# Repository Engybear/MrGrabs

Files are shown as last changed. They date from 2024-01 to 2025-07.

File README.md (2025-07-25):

# MrGrabs
<div align = "center"> 
  
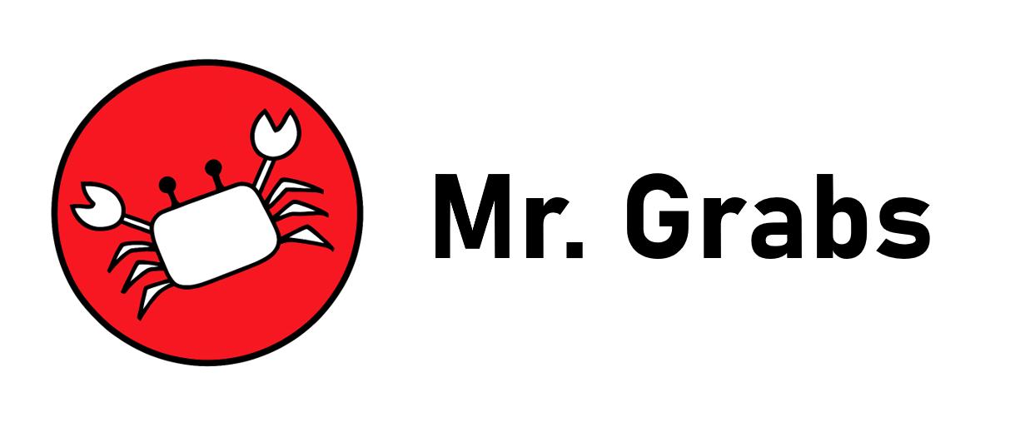
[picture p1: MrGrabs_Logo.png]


</div>

<!-- TOC -->
* [MrGrabs](#mrgrabs)
  * [Inspiration, Purpose and Goals](#inspiration-purpose-and-goals)
  * [What It Does / Overview](#what-it-does--overview)
  * [File Organization / How It's Made](#file-organization--how-its-made)
  * [Challenges Faced](#challenges-faced)
  * [Accomplishments To Be Proud Of](#accomplishments-to-be-proud-of)
  * [Next Steps](#next-steps)

## Inspiration, Purpose and Goals
This project was inspired by a professor's desire to ride around the University of Toronto campus inside and outside buildings on a robot that could wave to students with mechanical arms.

After scaling down the scope of the project to fit within a provided budget of $1000, the primary objective of this project was to build a robot that would complement another research project that involved the use of artificial intelligence for facial and voice recognition on a computer. With this in mind, the robot was designed with a laptop mount, but to further ability to interact with humans, it was also given the capability to navigate through conventional doorways inside buildings of the university campus and to mechanically interact with humans through pre-programmed robotic arm gestures. 

As a secondary objective during construction, the approach of pushing the limits of the quality of the final product with as minimal expense as possible was taken.

## What It Does / Overview
MrGrabs is a medium-sized (16x16x20'') robot, capable of driving through doors with at lest 2' of clearance. It is built primarily out of PLA, with plexiglass and wood used to reinforce the chassis. The robot is controlled via a custom bluetooth APP on an Andriod phone, and integrated with a Microsoft Surface Pro running an application of another project to scan for, greet and wave to students on campus. It also has four HC-SR04 Ultrasonic Sensors that are unused but intended to be a safety feature to prevent collisions.

<div align="center">
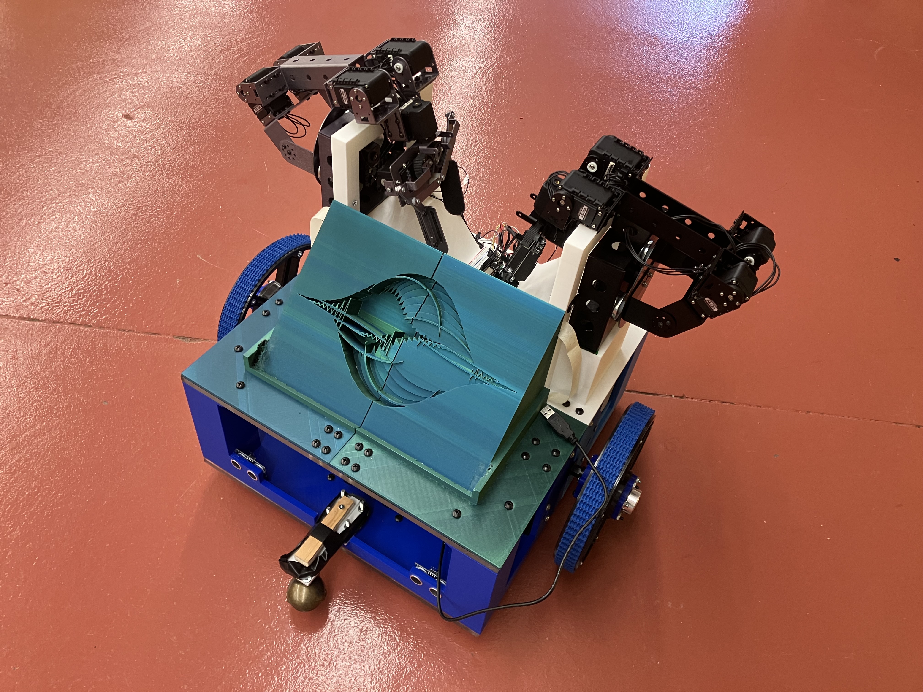
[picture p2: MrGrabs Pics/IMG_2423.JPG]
  
  
</div>

### Design Breakdown
Here you can see an overview of the design. The phone connects to the principal controller of the robot (Arduino Nano 33 BLE), which directly manages the motors through the IRF3205. There are also 2 agent controllers, as the Adafruit Feather 32u4 BluefruitLE, that receive simple commands from the principal controller, which are individually used to control the 2 robotic arms, made up of 7 daisy chained AX12-A servos. The Arduino Nano itself is powered by and can recieve data from a mounted laptop, if desired. Lastly, there are HC-SR04 sensors that can be controlled by the Arduino Nano as well to lock up the motors if a collision is imminent.

<div align = "center"> 
  
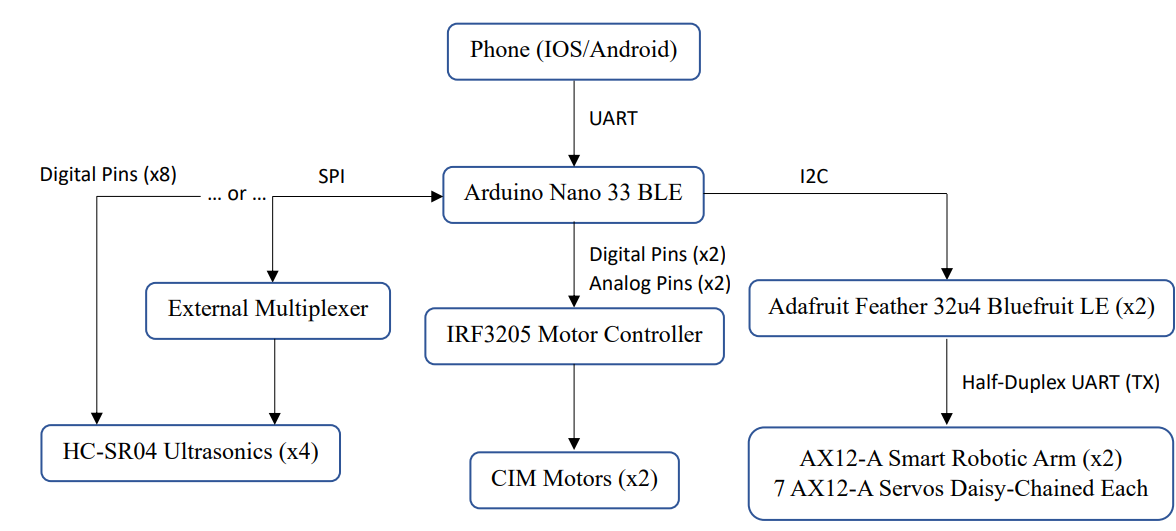
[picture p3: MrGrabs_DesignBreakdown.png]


</div>

- Refer to MrGrabs Pics for more images of the robot

## File Organization / How It's Made

Refer to User Guide for setup and usage information

Refer to Construction Guide for system design information

Refer to ArduinoCode/MainSketches for the code controlling the robot's code written in `C++`

Refer to BluetoothApp for the BLE5.aia file used to configure the andriod app remote controller created through `MIT App Inventor`

Refer to Step and Print files for CAD design and 3D printing files created in `Fusion360`

## Challenges Faced
The major challenge during the construction of the robot was maintaining a low budget while designing the robot’s chassis to support the forces it would experience. Although the original design was entirely 3D printed plastic, additional materials of plexiglass and wood were scavenged and machined to be worked into the robot’s design. The plexiglass was required because the weight of the robot's components would bend the plastic. The wood was required after the original high-density plastic mounts for the castor wheels snapped under both the weight and the torque of the robot starting and stopping motion.

Another challenge faced was the timeline given to develop the robot being 6 weeks. That is 6 weeks to plan the design, 3D model, 3D print, physically acquire, construct, and machine the chassis and its components parts, program multiple on-board controllers in an embedded system, build a remote bluetooth controller app from scratch, do the final stages of testing, making adjustments / deal with setbacks where needed and finally write up the documentation / user guides. Needless to say, the design isn't perfect. The motors were over-engineered and can go much, much faster than the robot needs to under its current weigh of ~30lbs, while the supports for the castor wheels under-engineering and snapped during intitial tests.

Lastly, it should be noted that the robotic arms were taking from a lab that had shelved them, from being outdated. They are at least 10 years old and during operation if the robot moved to quickly while the arms were not stowed, the arms' servos would not be able to hold up their own weight or complete their set path while under external torques. Additionally, with the equipment I had available, I was only able to create a half-dupliex communication line between the Adafruit boards and the robotic arms, to either read current positions or set goal positions. not both at the same time. As such the Adafruit boards had to rely on delays to roughly estimate when a motion would be complete, compounding on the limitations of the robotic arms in the design.

## Accomplishments To Be Proud Of
With this being only my second year of university, this was my first attempt at solo-developing a robot, first time trying to print something this big, first time creating a bluetooth controller app, and many other firsts (granted many thanks are owed to the people who provided me with the resources and advice to make this happen), I believe it's an accomplishment in and of itself to have finished a working design within both the set budget and timeline.

It pleases me to know that 2 years later, the project has not been shelved but been passed on to another research student who is working on extending the chassis in height to make the robot larger and more humanoid and fully integrate the sensors and AI code into the controller for the robot. It is possible that we might see a prototype rolling around the university campus in the summer or a capstone team working on the design, as the project continues to develop towards an interactable lecture attendance keeper.

## Next Steps
1.	It is HIGHLY recommended in the future that for a project of this scale, to allot more than 6 weeks and a single person to work on the project, for the sake of allowing more time to think through the design in its initial phases, different ideas to come up from different people, and minimize oversights.
2.	It is HIGHLY recommended that stronger mounts for castor wheels are designed in any new design iterations of this robot, as that is the robot’s biggest current design weakness and point of failure during operation.
3.	It is HIGHLY recommended that if the design is to be 3D printed again, methods be implemented to reduce the use of supports as much as possible, while taking into consideration the structural integrity of the design. Reducing the use of supports, both reduces the costs spent on materials and reduces the printing time of each piece, which can make the difference between printing 1 piece or 2 pieces in a single day. Talk to the person who is managing the 3D printer you want to use, for ideas.
4.	It is recommended to look into methods of recharging the robot’s 12V and 4V battery, as the Energy Systems Lab currently does not have a battery charger, as of 2023. The professor has stated that using a DC power supply to charge the battery is viable.
5.	It is recommended to invest in a Roborio for both now and all future projects, rather than using Arduino or Adafruit boards, as a Roborio can support several different kinds of I/O at a processing speed much faster than an Arduino/Adafruit board would be able to provide.
6.	It is recommended to swap out the bolts on the bottom of the robot for shorter 1’’ ones to allow for more clearance underneath the robot.
7.	It is recommended to find a different method of wiring hardware parts of the robot together, as to not use cheap/old jumper wires and solder to hold them together under heat shrink.
8.	It is also recommended in future design iterations to allow more time to think about wiring and include design features like hooks to help secure wires down.
9.	It is recommended that if the Ultrasonics Sensors are to be wired up to the Arduino Nano 33 BLE board, that an additional SPI multiplexer chip is used to reduce the number of digital pins used up by the Nano. This is to leave room for potential future additions.

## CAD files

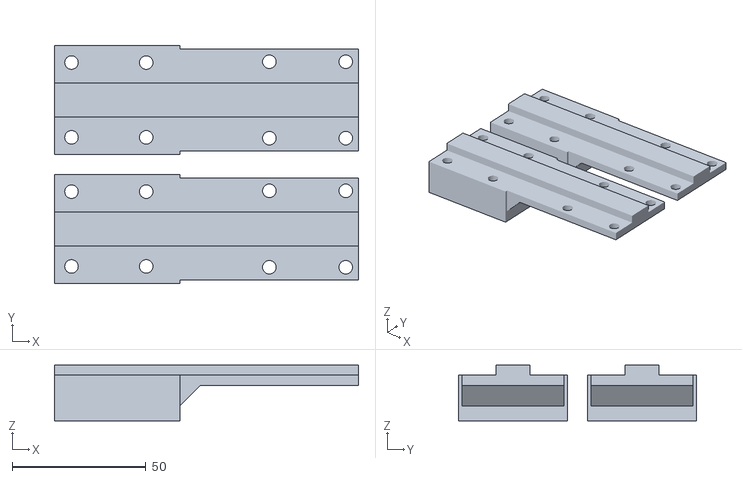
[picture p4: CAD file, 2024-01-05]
CAD_PrintFiles/MountsSection2.stl
113.7 x 88.9 x 20.9

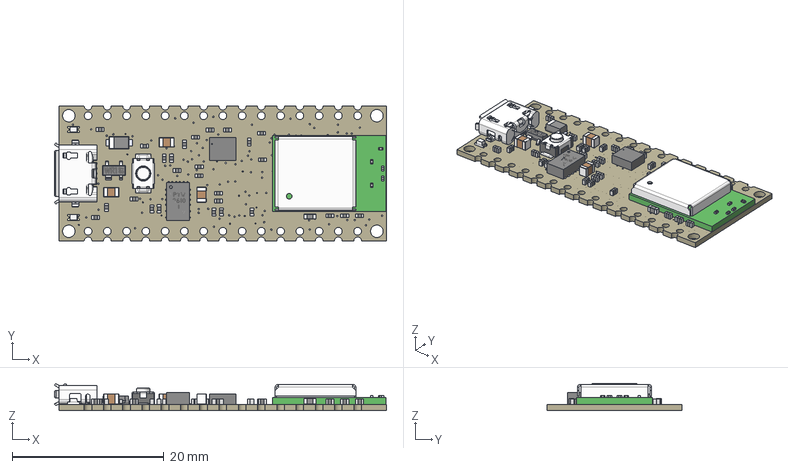
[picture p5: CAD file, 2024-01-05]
CAD_StepFiles/Nano33BLE.step
43.8 x 17.8 x 3.57 mm
Board (1)
LSM9DS1TR_LGA-24_3X3P5X1_STM v1
ZX62-AB-5PA (1)
IoT_HSMG-C190 LED v1 x 2
IoT_MPM3610 Step-Down Module v1
User Library-arduino_nano_reset core
User Library-arduino_nano_reset shell
RC0402FR-071KL RC0402N_YAG v1 x 27
BLM18EG101TN1D v1
C0805C472KDRACTU v1 x 3
PMEG6020AELRX v1
IoT_PRTR5V0U2X Protection Diode v1
NINA-B306-00B-00--3DModel-STEP-56544 v1

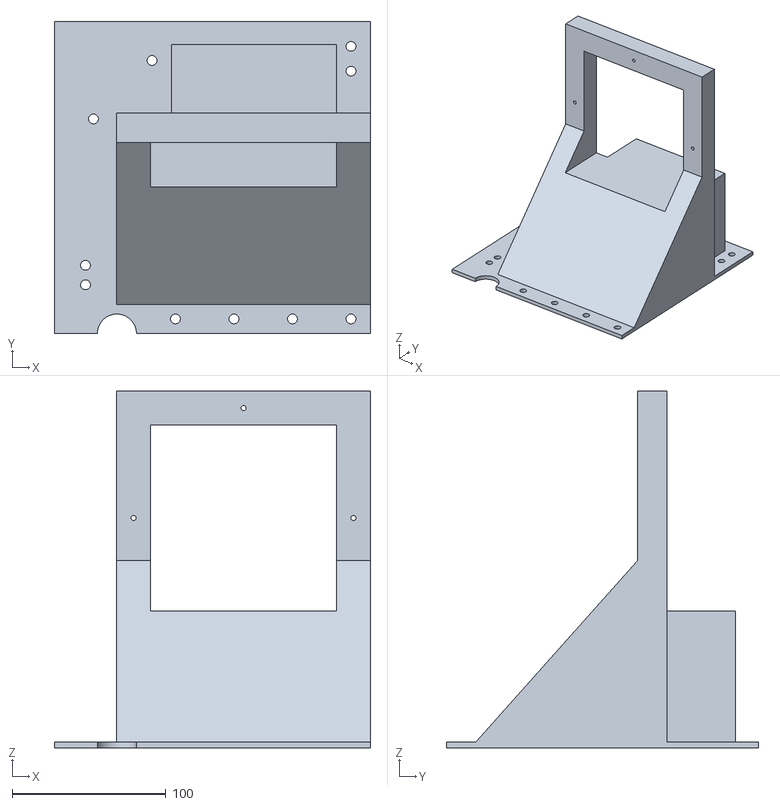
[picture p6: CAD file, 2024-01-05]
CAD_PrintFiles/LeftHalfTorsoSection.stl
205.7 x 203.2 x 232.4

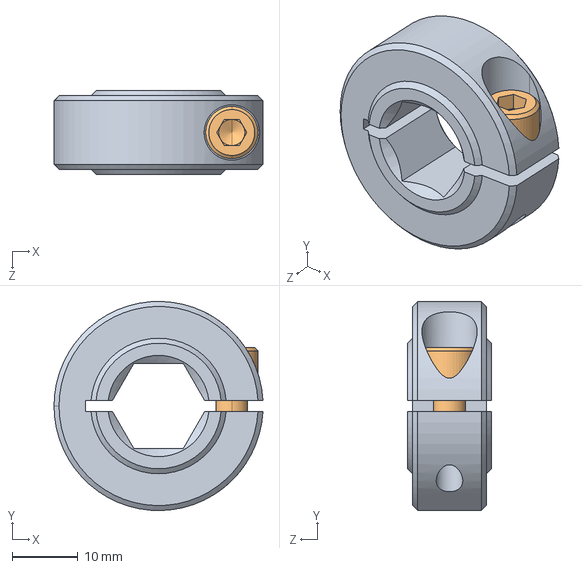
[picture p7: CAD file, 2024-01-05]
CAD_StepFiles/am-1526 500Hex HD Collar Clamp.STEP
31.7 x 31.7 x 12.7 mm
am-1238a 500Hex Collar Clamp Body
10-32x0500_shcs_HX-SHCS 0.19-32x1.375x1-C

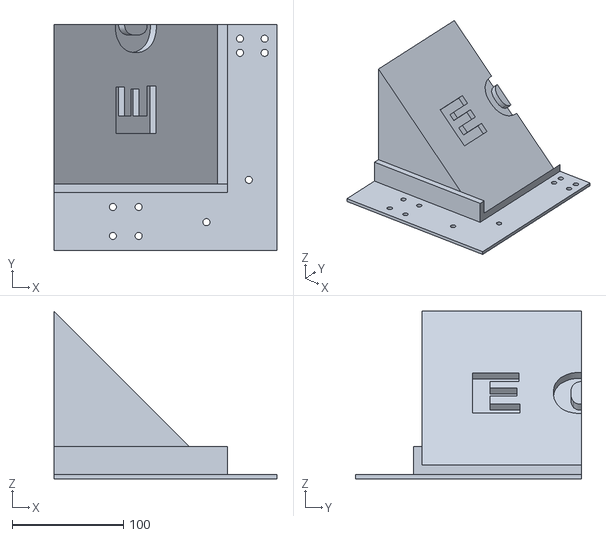
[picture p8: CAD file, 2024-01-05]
CAD_PrintFiles/TorsoSimpleLogoHalf2.stl
200.7 x 203.2 x 151.1

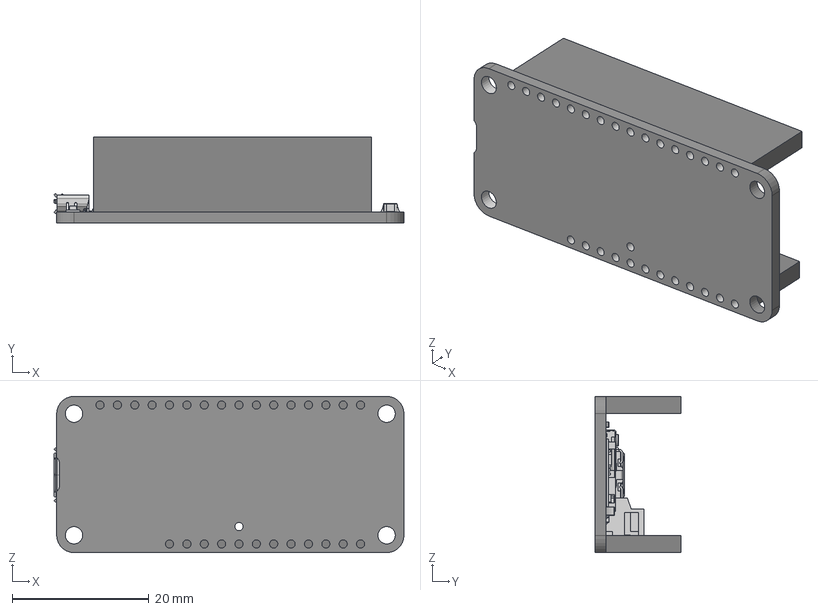
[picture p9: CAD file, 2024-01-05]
CAD_StepFiles/BlueFeather.step
51.2 x 12.6 x 22.9 mm
board
P0
P0 solder
pin x 2
mount x 2
housing
TSOP-5 v3 x 2
cap0805_05 v2 x 5
cap0805_03 v2
cap0603_03 v3 x 2
smt_tact_button v3
resistor_0603 v2 x 7
package
lead x 4
lead (mirror) x 4
smt_led_0805 v2 x 2
Short Board Connector
Long Board Connector

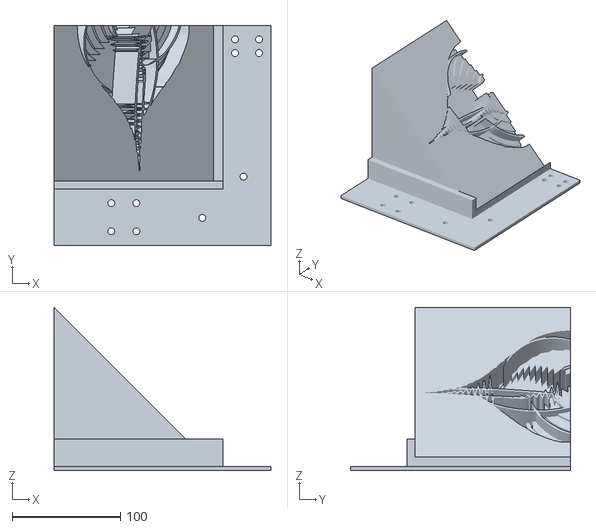
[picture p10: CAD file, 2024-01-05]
CAD_PrintFiles/TorsoFancyLogoHalf1.stl
200.7 x 203.2 x 151.1

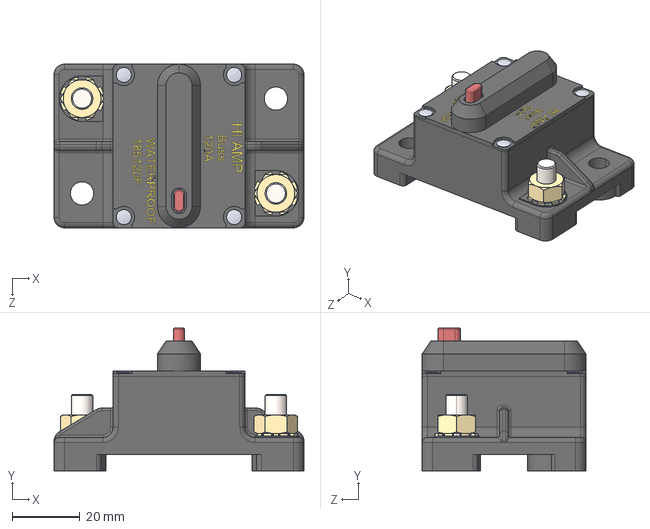
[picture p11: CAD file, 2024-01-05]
CAD_StepFiles/am-0282 120a Circuit Breaker.STEP
73.7 x 42.1 x 48.3 mm

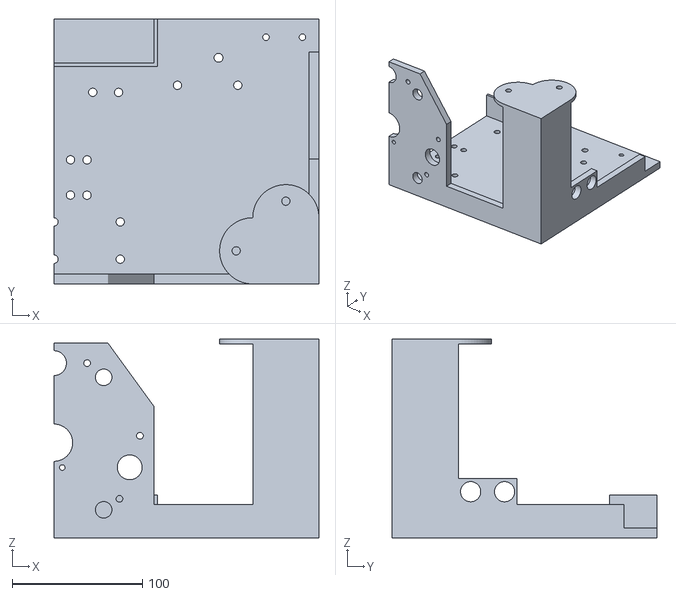
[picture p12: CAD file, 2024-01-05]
CAD_PrintFiles/BaseSection2.stl
203.2 x 203.2 x 152.4

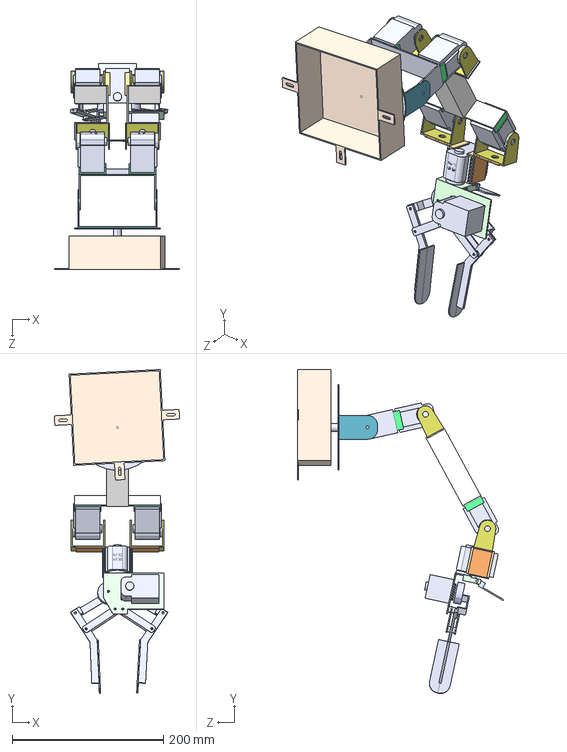
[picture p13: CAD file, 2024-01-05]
CAD_StepFiles/AX12-18 Smart Arm.IGS
165.8 x 429.0 x 273.2 mm

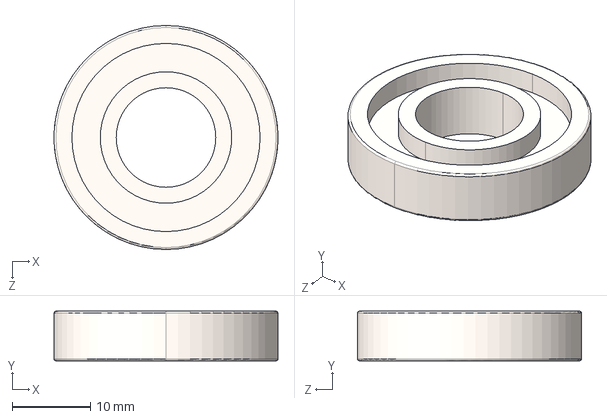
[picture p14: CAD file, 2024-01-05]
CAD_StepFiles/am-0029 0.5'' id Bearing (R8).STEP
28.6 x 6.32 x 28.6 mm

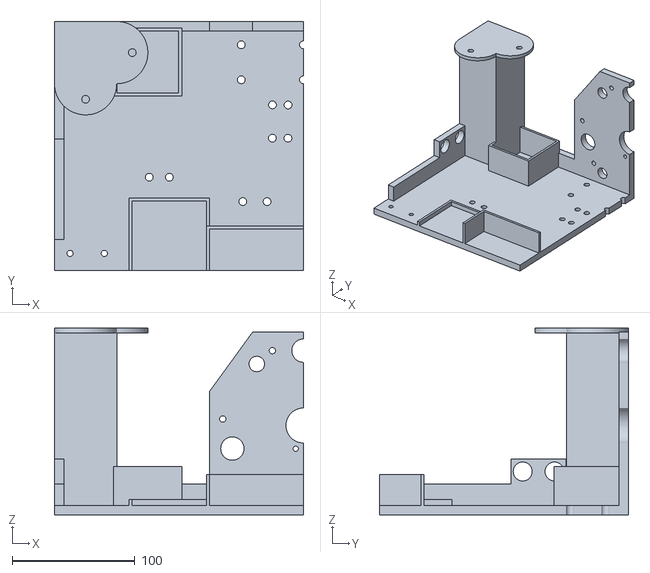
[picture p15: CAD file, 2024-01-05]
CAD_PrintFiles/BaseSection3.stl
203.2 x 203.2 x 152.4

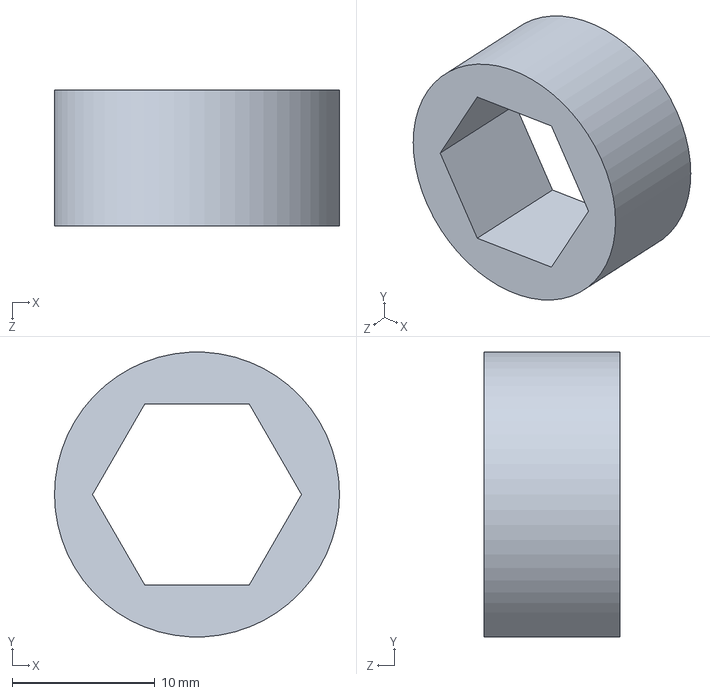
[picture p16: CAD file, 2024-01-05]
CAD_StepFiles/am-3948-375 500H x 375IN Spacer.STEP
20.0 x 20.0 x 9.53 mm

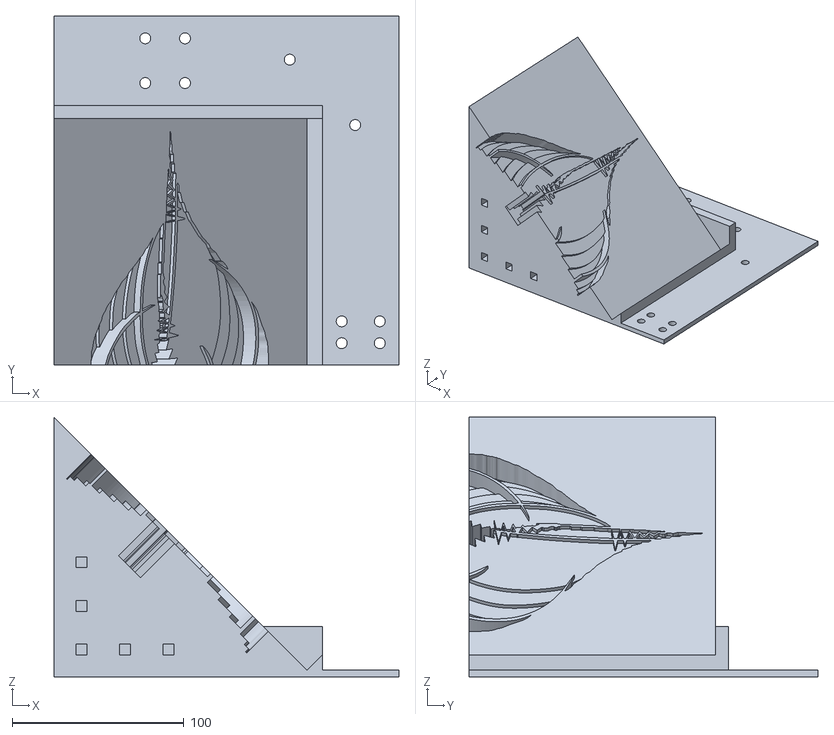
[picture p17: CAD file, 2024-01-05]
CAD_PrintFiles/TorsoFancyLogoHalf2.stl
200.7 x 203.2 x 151.1

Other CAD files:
CAD_PrintFiles/RightHalfTorsoSection.stl
CAD_StepFiles/am-3316 6 inch Plaction Wheel with Roughtop.STEP
CAD_PrintFiles/TorsoSimpleLogoHalf1.stl
CAD_StepFiles/am-4124 500 Hex Hub.STEP
CAD_PrintFiles/BaseSection1.stl
CAD_PrintFiles/BaseSection4.stl
CAD_PrintFiles/MountsSection1.stl
CAD_StepFiles/HCSR04 Ultrasonic Sensor.STEP

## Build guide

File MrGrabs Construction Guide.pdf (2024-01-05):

## Robot Project: Mr. Grabs’ Construction Guide

Nicholas Mutlak

University of Toronto

August 31st, 2023

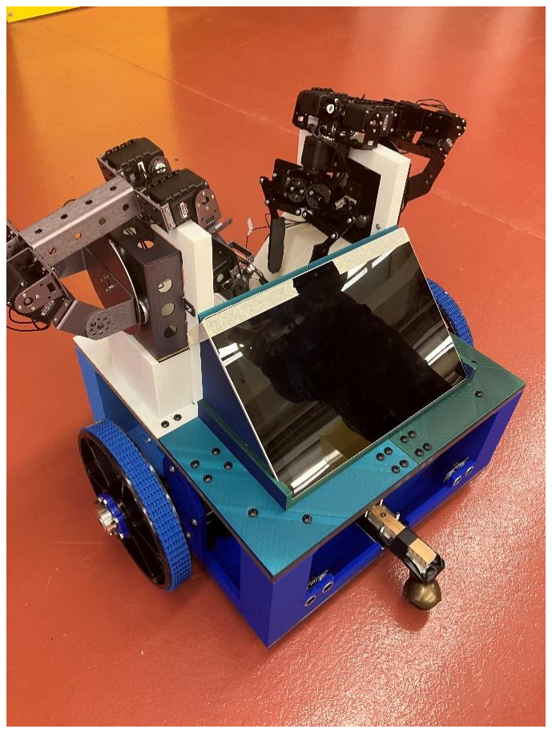
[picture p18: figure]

Introduction

During the summer of 2023, a robot that will be referred to as ‘Mr. Grabs’ was designed, built, and programmed in a 6-week timeline. The purpose of this robot was to accompany a separate project being developed on a computer by another student, that would involve both facial and voice recognition and interaction with human beings. The robot would allow for the computer of that project to be mounted onto it, and from there make the features of that project mobile and more expressive through the use of mechanical arms. This guide entails details about the robot’s design process, construction, and programming.

Parts List

Part | Qty | Link
Vex Robotics SS Gearbox, 84:12 | 1 | https://www.vexrobotics.com/single-speed-single-reduction.html (https://www.vexrobotics.com/single-speed-single-reduction.html)
CIM Motor | 2 | https://www.andymark.com/products/2-5-in-cim-motor (https://www.andymark.com/products/2-5-in-cim-motor)
8’’ Plaction Wheels | 2 | https://www.andymark.com/products/8-in-plaction-wheel-with-blue-nitrile-tread (https://www.andymark.com/products/8-in-plaction-wheel-with-blue-nitrile-tread)
1.5’’ Castor Wheels | 2 | https://www.amazon.ca/Caster-Wheels-Furniture-Profile-Roller-Included/dp/B07T8NMYFZ (https://www.amazon.ca/Caster-Wheels-Furniture-Profile-Roller-Included/dp/B07T8NMYFZ)
½ Hex Spacers | 8 | AndyMark
½ Hex Shaft Collars | 2 | AndyMark
Motor Controller (FAULTY) | 1 | https://www.amazon.ca/H-Bridge-Control-IRF3205-Response-Arduino/dp/B08JM4Z1HP (https://www.amazon.ca/H-Bridge-Control-IRF3205-Response-Arduino/dp/B08JM4Z1HP)
Arduino Nano 33 BLE | 1 | https://store-usa.arduino.cc/products/arduino-nano-33-ble (https://store-usa.arduino.cc/products/arduino-nano-33-ble)
Adafruit Feather 32u4 Bluefruit LE | 2 | https://www.adafruit.com/product/2829
30A Breaker | 1 | https://www.amazon.ca/iplusmile-Circuit-Breaker-Manual-Marine/dp/B086X2SZL2 (https://www.amazon.ca/iplusmile-Circuit-Breaker-Manual-Marine/dp/B086X2SZL2)
12V Battery | 1 | https://batteryclerk.ca/products/sigmastek-sp12-7-5-12v-7ah-sealed-lead-acid-replacement-battery (https://batteryclerk.ca/products/sigmastek-sp12-7-5-12v-7ah-sealed-lead-acid-replacement-battery)
4V Battery | 1 | https://www.amazon.ca/Volt-Sealed-Lead-Acid-Battery/dp/B00ZCPF274 (https://www.amazon.ca/Volt-Sealed-Lead-Acid-Battery/dp/B00ZCPF274)
HC-SR04 Ultrasonic Sensors | 4 | https://www.digikey.ca/en/products/detail/adafruit-industries-llc/3942/9658069 (https://www.digikey.ca/en/products/detail/adafruit-industries-llc/3942/9658069)
AX12-A Smart Robotic Arm | 2 | https://www.crustcrawler.com/products/AX12A%20Smart%20Robotic%20Arm/ (https://www.crustcrawler.com/products/AX12A%20Smart%20Robotic%20Arm/)
Android Phone | 1 | Borrowed (provided by students)
Microsoft Surface Pro 7 | 1 | Borrowed (provided by students)
Assortment of 10-32 Screws | 125+ | Amazon

The chassis on which all these parts rest on, was 3D printed by a Bambu Lab X1 Carbon 3D Printer in eight, 8x8’’ sections, for a full 16x16’’ chassis. Two sheets of 16x16’’ quarter inch thick plexiglass were used to secure the 3D printed chassis together with machine screws and nuts.

In addition to the main body, mounts for the castor wheels where printed after a few design iterations. These mounts were not successful in upholding the weight of the robot. A splint made out of wood, a stronger material than the 15% infill plastic mount, was designed to fix this problem.

The files for the 3D print design were made in Fusion360, which you can find in the CAD_PrintFiles folder. The CAD models these designs were made around can be found in the CAD_StepFiles folder.

Communication Setup

The robot was designed to have the following parts talk to each other through different

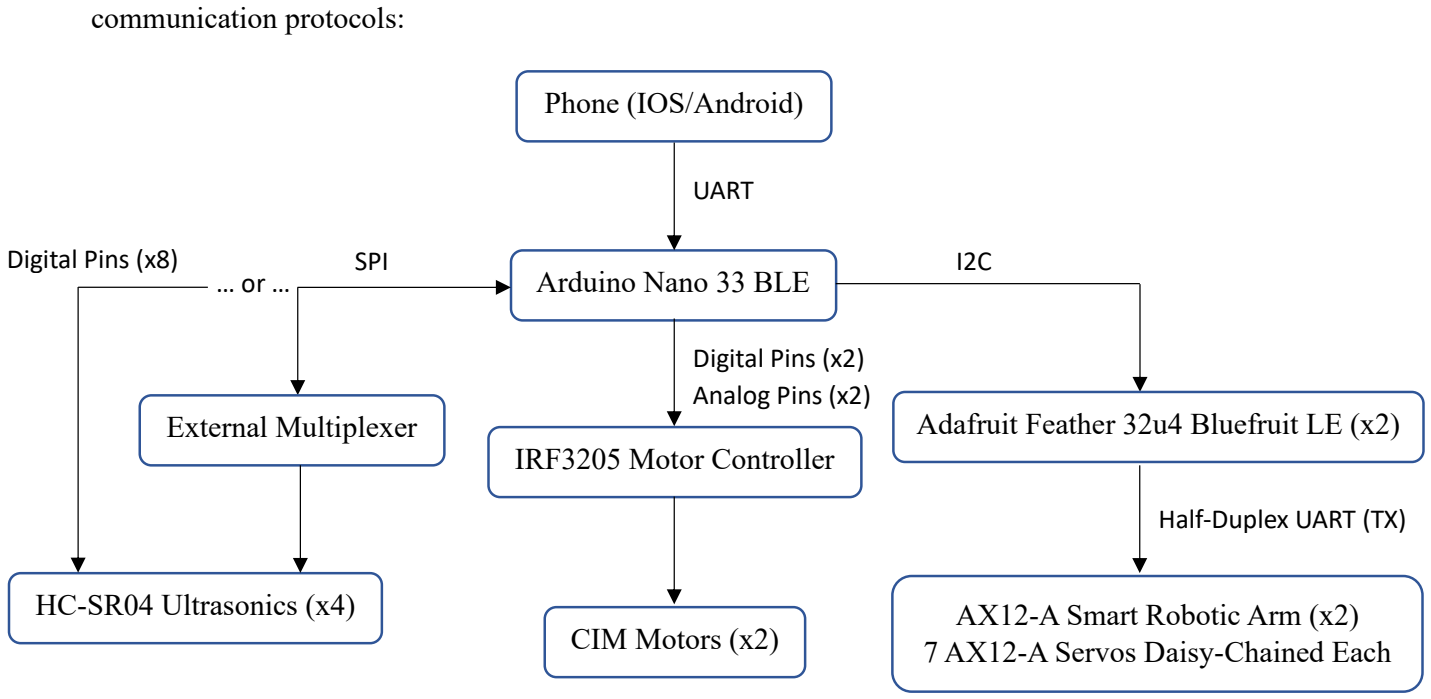
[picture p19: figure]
communication protocols:; Phone (IOS/Android); Arduino Nano 33 BLE; UART; Digital Pins (x2) Analog Pins (x2); IRF3205 Motor Controller; CIM Motors (x2); HC-SR04 Ultrasonics (x4); External Multiplexer; SPI; Digital Pins (x8); Adafruit Feather 32u4 Bluefruit LE (x2); Half-Duplex UART (TX); AX12-A Smart Robotic Arm (x2) 7 AX12-A Servos Daisy-Chained Each

Applications made through MIT App Inventor are compatible with both IOS and Android devices, however the BLE extension used for the app, is not compatible with IOS devices as of 2023. From the bluetooth app, the phone would connect wirelessly with the Arduino Nano 33 BLE, with its UART pins. Using two digital and analog pins, the Arduino Nano 33 BLE would interpret signals from the app to control the CIM motors through the IRF3205 Motor Controller.

For actions related to the mechanical arms sent from the app, the Arduino Nano 33 BLE would send signals through I2C communication protocol to the two Adafruit Feather 32u4 Bluefruit LE boards. The Adafruit boards would then interpret those signals and transmit machine code instructions through a packet handler to the 7 daisy-chained AX12-A servos that control the arms movement. It should be noted that due to limitations of the Adafruit boards, they are only able to either send bytes (TX) or receive bytes (RX) during runtime, and are not able to do both. This means the Adafruit boards are not able to read information like a servo’s position, and as such from a programming side, resulting in having to resort to using delays to make an educated guess when the arm will have finished moving to a new position during runtime.

Lastly the robot comes equipped with four HC-SR04 Ultrasonic Sensors. Due to lack of time and additionally having the unanswered question of, “If the Arduino Nano 33 BLE is reading from four ultrasonic sensors sequentially through polling would it slow down the control of the robot too much?” the sensors were left unwired. It was intended for them to be used as emergency stops, to ensure the robot does not crash into objects during operation. To wire them up, two options were considered. Option 1 would be to use 8 digital pins, which the Arduino Nano 33 BLE can support. Option 2 would be to use SPI communication protocol with an external multiplexer that could be used for the chip select, as HC-SR04 do not have an internal chip select.

Programming

Arduino IDE was used to program in C++ and upload sketches stored as .ino files to all of the Arduino and Adafruit boards. The Arduino Nano 33 BLE has been uploaded the Main_Nano_Board.ino sketch, while the two Adafruit boards have been uploaded the Left_Arm_Adafruit_Board.ino and Right_Arm_Adafruit_Board.ino files with respect to how they are physically labelled on the robot. To upload a new sketch to any of the boards, connect a USB to a Micro-USB cable between the board and your computer, and upload via the Arduino IDE.

AX12-A Smart Robotic Arm

The AX12-A Smart Robotic Arms were acquired for 4th year robotics labs, at a minimum of 10 years ago. The labs were designed for Matlab, and documentation regarding them has been lost. The setup guide to put build an arm from a kit that comes with the AX12-A Smart Robotic Arm, should be stored with the robot.

The arms were purchased from CrustCrawler and documentation can be found here: https://www.crustcrawler.com/products/AX12A%20Smart%20Robotic%20Arm/

Further documentation about the AX12-A servos and how their control tables are setup can be found here: https://emanual.robotis.com/docs/en/dxl/ax/ax-12a/

Over the timeline of this robot project, there were two methods of interacting with the robotic arm. Method 1 was through Arduino/Adafruit boards using the AX12-A library for Arduino IDE, documentation about which can be found here: https://github.com/jumejume1/AX-12A-servolibrary. (https://github.com/jumejume1/AX-12A-servo-library) This method is somewhat lacking, as the Arduino/Adafruit boards used on the robot can only either read or send data through a TX or RX pin, but was necessary for the arms to be controlled independently of a computer.

Method 2 was through how the robotic arms were initially designed to function, with a USB2Dynamixel board and the Dynamixel Software Development Kit (SDK), which would allow a computer to interface with the robotic arm via Visual Studio Express. To do this requires a considerable larger amount of setup, for which documentation can be found here: https://emanual.robotis.com/docs/en/software/dynamixel/dynamixel_sdk/download/#repository and here:
https://emanual.robotis.com/docs/en/software/dynamixel/dynamixel_sdk/library_setup/cpp_windows/#cpp-windows. (https://emanual.robotis.com/docs/en/software/dynamixel/dynamixel_sdk/library_setup/cpp_windows/)

The benefit of this method is the USB2Dynamixel board is able to both write and read data to the arms during runtime. This was used to manipulate primarily to manipulate arms into desired positions by hand, and then read the position of each arm and record them as states the arm would be in during operation.

In addition to either of these methods, it is necessary to use a computer with a USB2Dynamixel to set the baud rate and ids of any new-out-of-the-box servos to 1,000,000 and 1 through 7 in the daisy chain, if you are building a new robotic arm. This requires the installation of RoboPlus and use of the Dynamixel Wizard, documentation on which can be found here: https://robotis.co.uk/software/roboplus-1-0.html and here: https://emanual.robotis.com/docs/en/software/rplus1/dynamixel_wizard/.

Bluetooth App

There are several applications on IOS that can connect to an Arduino and interact with it, however there were none that provided a decent controller interface, were free, and worked with the Arduino Nano 33 BLE specifically. As such, a custom bluetooth app was created using MIT App Inventor. To build your own app using the MIT App Inventor code block sketch interface or better understand the design of BLE5.aia already made for this project, refer to this tutorial: https://www.youtube.com/watch?v=RvbWl8rZOoQ to get started. It should be noted that BLE5.aia project makes use of more than what the basic tutorial provided covers. As such, further documentation about the BluetoothLE extension used for the project can be found here: https://iot.appinventor.mit.edu/#/bluetoothle/bluetoothleintro

Recommendations for the Future

1. It is HIGHLY recommended in the future that for a project of this scale, to allot more than 6 weeks and a single person to work on the project, for the sake of allowing more time to think through the design in its initial phases, different ideas to come up from different people, and minimize oversights.
2. It is HIGHLY recommended that stronger mounts for castor wheels are designed in any new design iterations of this robot, as that is the robot’s biggest current design weakness and point of failure during operation.
3. It is HIGHLY recommended that if the design is to be 3D printed again, methods be implemented to reduce the use of supports as much as possible, while taking into consideration the structural integrity of the design. Reducing the use of supports, both reduces the costs spent on materials and reduces the printing time of each piece, which can make the difference between printing 1 piece or 2 pieces in a single day. Talk to the person who is managing the 3D printer you want to use, for ideas.
4. It is recommended to look into methods of recharging the robot’s 12V and 4V battery, as the Energy Systems Lab currently does not have a battery charger, as of 2023. The professor has stated that using a DC power supply to charge the battery is viable.
5. It is recommended to invest in a Roborio for both now and all future projects, rather than using Arduino or Adafruit boards, as a Roborio can support several different kinds of I/O at a processing speed much faster than an Arduino/Adafruit board would be able to provide.
6. It is recommended to swap out the bolts on the bottom of the robot for shorter 1’’ ones to allow for more clearance underneath the robot.
7. It is recommended to find a different method of wiring hardware parts of the robot together, as to not use cheap/old jumper wires and solder to hold them together under heat shrink.
8. It is also recommended in future design iterations to allow more time to think about wiring and include design features like hooks to help secure wires down.
9. It is recommended that if the Ultrasonics Sensors are to be wired up to the Arduino Nano 33 BLE board, that an additional SPI multiplexer chip is used to reduce the number of digital pins used up by the Nano. This is to leave room for potential future additions.

Special Thanks

This section is a thank you to all the people that helped make the completion of this project possible, and can also be used as a list of potential resources for new students working on this robot.

Thank you to:

- Professor Hamid Shokrollah-Timorabadi for providing the funding required to build the robot and a good sense of humor.
- Iman Koohi for allowing the use of his 3D printer and materials.
- Michael Colacci for allowing full use of his tools, supplies, and advice.
- Mehrdad Mehramiz for providing the mechanical arms used on the robot.
- Ryan Seto for providing integral advice with regard to 3D modelling and designing the robot.
- Simon Xu for providing manual assistance in putting the robot together.
- Shuntaro Wakamatsu for creating the logo displayed on the robot.

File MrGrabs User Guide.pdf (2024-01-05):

## Robot Project: Mr. Grabs’ User Guide

Nicholas Mutlak

University of Toronto

August 31st, 2023


Introduction

During the summer of 2023, a robot that will be referred to as ‘Mr. Grabs’ was designed, built, and programmed in a 6-week timeline. The purpose of this robot was to accompany a separate project being developed on a computer by another student, that would involve both facial and voice recognition and interaction with human beings. The robot would allow for the computer of that project to be mounted onto it, and from there make the features of that project mobile and more expressive through the use of mechanical arms. This guide entails how to use the robot.

Step-by-Step Setup Guide for New Users

In order to control the robot, you will need:

1. An android phone to use as your controller, as well as another device of any kind with access to the internet.

On your computer or separate device:

2. Go to “ai2.appinventor.mit.edu/” and create an account.
3. Import the BLE5.aia file, under the BluetoothApp folder, to a new project MIT App Inventor (refer to Figure 1)

On your android phone:

4. On the android PlayStore, install the app: MIT AI2 Companion (refer to Figure 4)
5. Pair phone with computer’s MIT App Inventor online sketch (refer to Figure 2, 3 and 5)

On your robot:

6. Plug in the 4V power supply line to power the Adafruit Feather 32u4 Bluefruit LE boards (refer to Figure 6a and 6b)
7. Plug in the 5V USB power supply for the Arduino Nano 33 BLE (refer to Figure 7a and 7b)
8. Close the breaker to connect the 12V power supply line (refer to Figure 8)

Finally:

9. Connect to the Arduino Nano 33 BLE via the bluetooth app on the android phone.

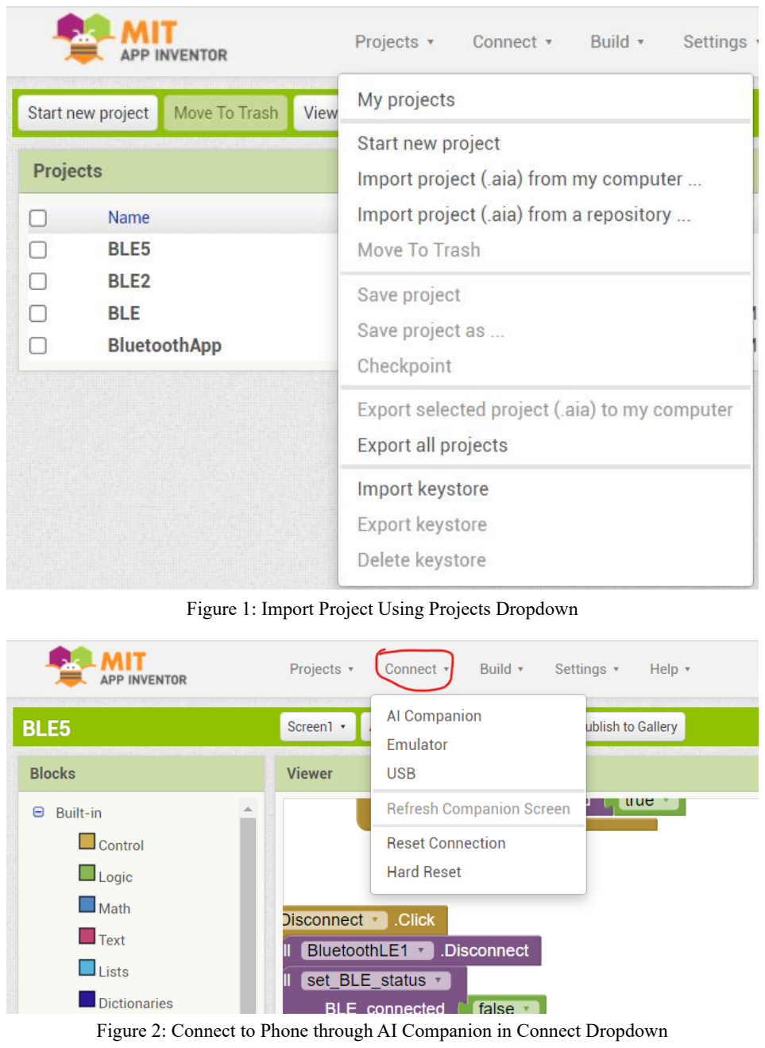
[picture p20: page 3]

Figure 1: Import Project Using Projects Dropdown

Figure 2: Connect to Phone through AI Companion in Connect Dropdown

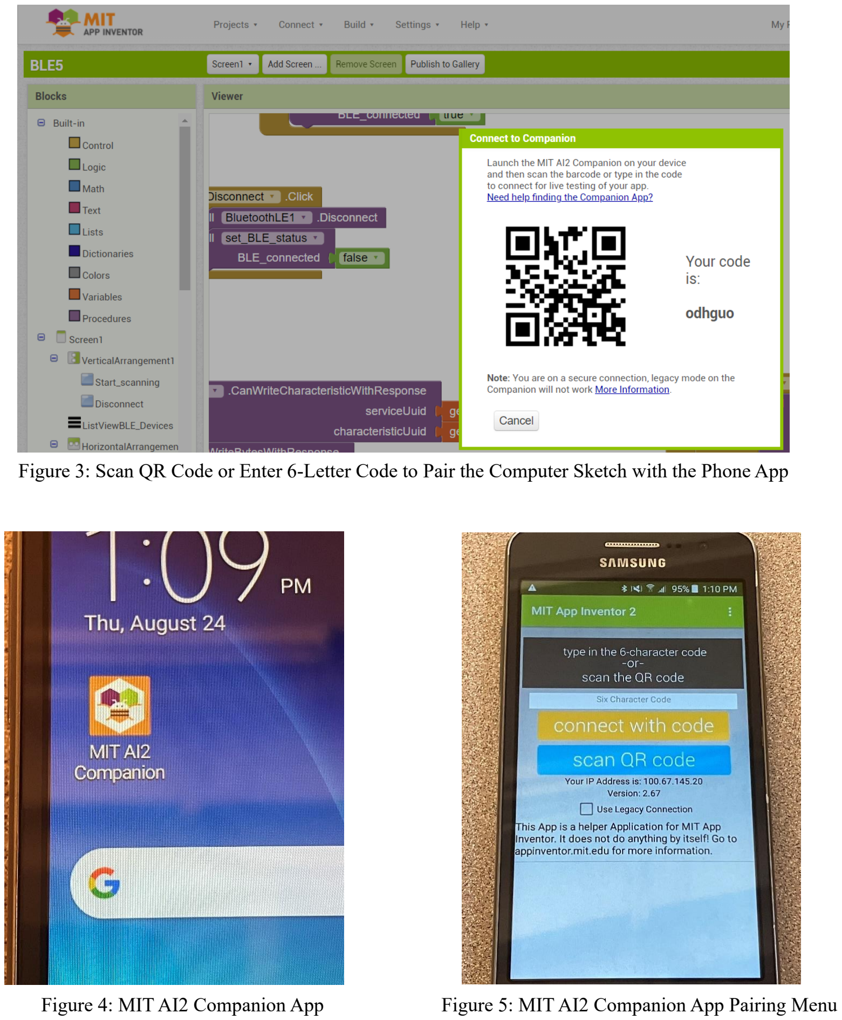
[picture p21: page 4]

Figure 3: Scan QR Code or Enter 6-Letter Code to Pair the Computer Sketch with the Phone App

Figure 4: MIT AI2 Companion App | Figure 5: MIT AI2 Companion App Pairing Menu

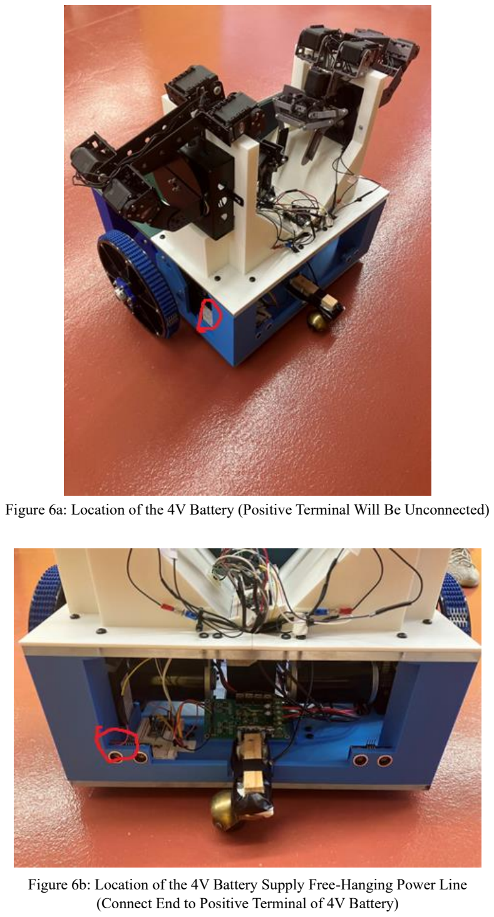
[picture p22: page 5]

Figure 6a: Location of the 4V Battery (Positive Terminal Will Be Unconnected)

Figure 6b: Location of the 4V Battery Supply Free-Hanging Power Line (Connect End to Positive Terminal of 4V Battery)

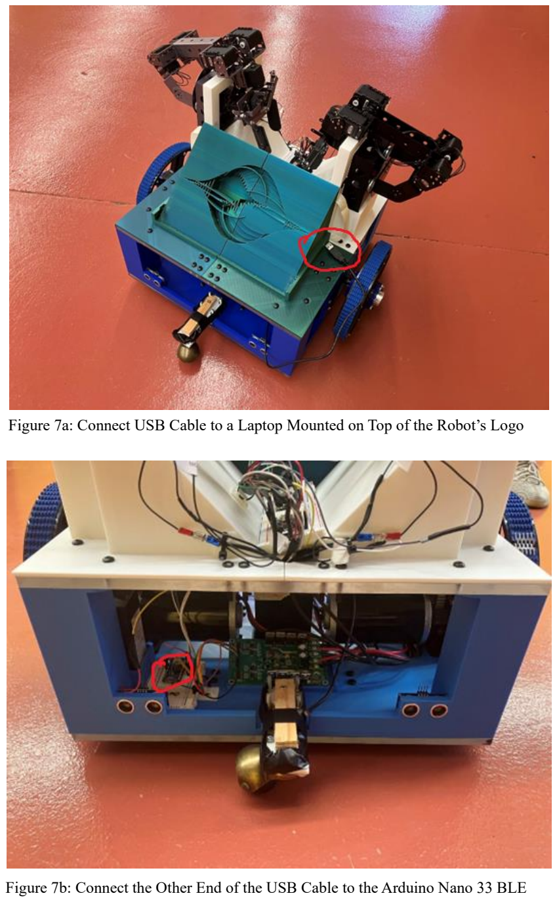
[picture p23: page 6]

Figure 7a: Connect USB Cable to a Laptop Mounted on Top of the Robot’s Logo

Figure 7b: Connect the Other End of the USB Cable to the Arduino Nano 33 BLE

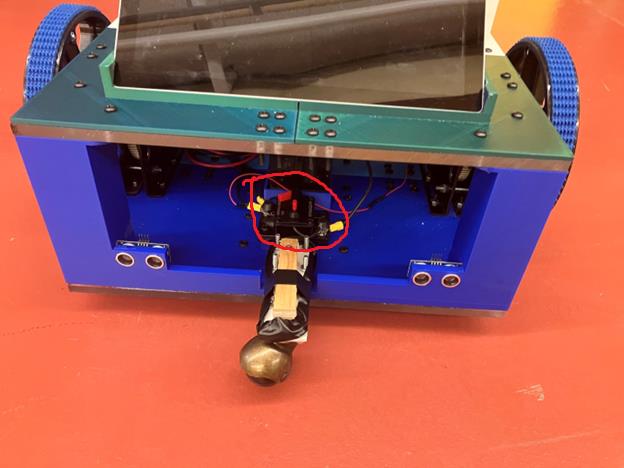
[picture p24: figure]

Figure 8: Location of the 30A Breaker

Bluetooth App Controller

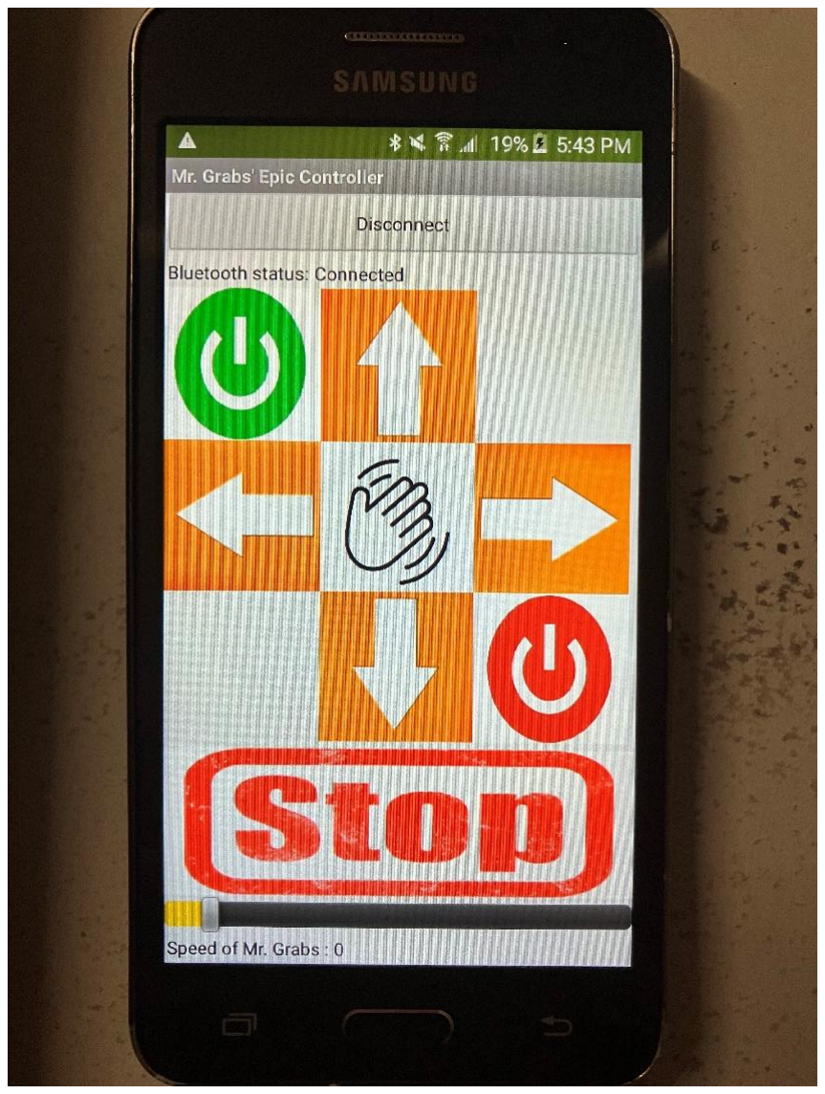
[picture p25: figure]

Wheel Movement Options:

- Up Arrow – Updates Speed and Direction of Wheels to Forwards
- Down Arrow – Updates Speed and Direction to of Wheels to Backwards
- Left Arrow – Updates Speed and Direction to of Wheels to Left
- Right Arrow – Updates Speed and Direction to of Wheels to Right
- STOP Button – Updates Speed of Wheels to 0
- Slider – Sets, but does not update, Speed of Wheels

Mechanical Arm Options:

- Green Startup Button – Tells Arms to move to their Undocked Position
- Wave Button – Will alternate between Arms, having them perform the Wave action
- Red Shutdown Button – Tells Arms to move to their Docked Position

# WARNINGS

1. DO NOT EXCEED a speed of 30 on the speed controller slider. The castor wheel mounts will not be able to withstand the force being applied to them when turning.
2. DO NOT SPAM the buttons. The Arduino Nano 33 BLE, although fast for an Arduino board, takes time to process each button press; Spamming buttons will cause instructions to pile up, especially with regard to the mechanical arms.
3. DO NOT DISCONNCT from the Arduino Nano 33 BLE board while the robot is in motion, as it will continue to be in motion. Ensure to hit the STOP button and stow away the mechanical arms before disconnecting from the Arduino Nano 33 BLE. This potential problem can be fixed with a ‘disconnect event handler’ if added to the Arduino Nano 33 BLE’s code.
4. Due to complications with the motorcontroller board only one of the wheels is able to spin backwards.
5. Due to complications with the silver mechanical arm’s first servo, it is not able to correct itself to keep the arm upright. It may fall down if the robot is in motion while the mechanical arms are not docked
6. When done using the robot, ensure to hit the breaker for the 12V battery, disconnect the positive terminal of the 4V battery, and disconnect the 5V USB power to the nano. The batteries using on the robot are rechargeable, but the lab does not have a battery charger.

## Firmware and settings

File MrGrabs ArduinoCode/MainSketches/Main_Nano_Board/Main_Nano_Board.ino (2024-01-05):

#include <Wire.h>
#define Left_Ada_Addr 5
#define Right_Ada_Addr 6

//RIGHT MOTOR
const int Motor1_Speed = A3; //orange - PWM2
const int Motor1_Dir = D3; //yellow - DIR2

//LEFT MOTOR
const int Motor2_Speed = A2; //green - PWM1 
const int Motor2_Dir = D2; //black - DIR1

#include <ArduinoBLE.h>
BLEService mainService("19B10010-E8F2-537E-4F6C-D104768A1214"); // create service
BLEByteCharacteristic buttonCharacteristic("19B10011-E8F2-537E-4F6C-D104768A1214", BLEWrite | BLERead | BLENotify); // allow remote device to write button presses
BLEByteCharacteristic speedCharacteristic("19B10012-E8F2-537E-4F6C-D104768A1214", BLEWrite | BLERead | BLENotify); // allow remote device to write speed slider value

//global speed value of motors + directions
int gCurSpeed1 = 0;
int gCurSpeed2 = 0;
int gSliderSpeed = 0;
bool curDir1 = HIGH; //HIGH = forward direction
bool curDir2 = HIGH; //HIGH = forward direction

//bool conditions for movement direction
bool movingBack = false;

void setup() {
  // put your setup code here, to run once:
  Serial.begin(9600);
  
  //start up BLE
  if(!BLE.begin()){
    Serial.println("Bluetooth startup failed");
    while(1);
  }

  //attach characteristics to main service
  BLE.setLocalName("MrGrabs");
  BLE.setAdvertisedService(mainService);
  mainService.addCharacteristic(buttonCharacteristic);
  mainService.addCharacteristic(speedCharacteristic);
  BLE.addService(mainService);

  //prep characteristics with interrupt handlers for button presses / slider updates
  buttonCharacteristic.writeValue(0);
  speedCharacteristic.writeValue(0);
  buttonCharacteristic.setEventHandler(BLEWritten, buttonValueHandler);
  speedCharacteristic.setEventHandler(BLEWritten, speedValueHandler);
  
  //advertist BLE service to public
  BLE.advertise();

  Wire.begin(); //setup as Main central for I2C

  //setup Adafruit boards as peripherals
  Wire.beginTransmission(Left_Ada_Addr);
  Wire.endTransmission();
  Wire.beginTransmission(Right_Ada_Addr);
  Wire.endTransmission();

  //setup motor control pins
  pinMode(Motor1_Speed, OUTPUT);
  pinMode(Motor1_Dir, OUTPUT);
  pinMode(Motor2_Speed, OUTPUT);
  pinMode(Motor2_Dir, OUTPUT);

  //initilize speed and direction to 0
  analogWrite(Motor1_Speed,gCurSpeed1);
  digitalWrite(Motor1_Dir,curDir1);
  analogWrite(Motor2_Speed,gCurSpeed2);
  digitalWrite(Motor2_Dir,curDir2);

}

/* Smooth Speed Changer function; used without flip to change speed, 
                                  used with flip twice, to decrement to 0, change direction pin, and then increment to desired negative direction value
 * curSpeed1 : current speed of Motor1
 * newSpeed1 : desired speed of Motor1
 * curSpeed2 : current speed of Motor2
 * newSpeed2 : desired speed of MOtor2
 * boolflip1 : Motor1's direction pin needs to flip
 * boolflip2 : Motor2's direction pin needs to flip
 */ 
void changeSpeedSmooth(int curSpeed1, int newSpeed1, int curSpeed2, int newSpeed2, bool flip1, bool flip2){
  // Serial.print("Updating Speed: ");
  // Serial.print(curSpeed1);
  // Serial.print(" -> ");
  // Serial.print(newSpeed1);
  // Serial.print(" / ");
  // Serial.print(curSpeed2);
  // Serial.print(" -> ");
  // Serial.print(newSpeed2);
  // Serial.print(" / flips: ");
  // Serial.print(flip1);
  // Serial.print(" / ");
  // Serial.println(flip2);

  int i = curSpeed1, j = curSpeed2;
  while(i != newSpeed1 || j != newSpeed2){
    if(i < newSpeed1) i++;
    else if(i > newSpeed1) i--;
    if(j < newSpeed2) j++;
    else if(j > newSpeed2) j--; 

    analogWrite(Motor1_Speed, i);
    analogWrite(Motor2_Speed, j);
    
    delay(10); 
    //delay is used to slow down the update of the speed to the motors 
    //this is to ensure we don't immediately jump from 0 to max speed and fry our motor controller
  }

  //update direction pins on flip condition
  if(flip1) digitalWrite(Motor1_Dir, curDir1);
  if(flip2) digitalWrite(Motor2_Dir, curDir2);
  delay(10);

  // Serial.print("Directions: ");
  // Serial.print(curDir1);
  // Serial.print(" , ");
  // Serial.println(curDir2);
  
  //update global speed values
  gCurSpeed1 = newSpeed1;
  gCurSpeed2 = newSpeed2;
}

bool armWave = true; //boolean to alternative between which arm will wave

void buttonValueHandler(BLEDevice central, BLECharacteristic buttonCharacteristic){ //will run when we receive a button press from the app
  byte data;
  int buttonValue = (int)(*buttonCharacteristic.value()); //receive the value being transmitted to us as an int

  switch (buttonValue){ //hardcoded cases based on which button was pressed
    case 1: //Move forwards
      //goal: Motor1_Speed = gSliderSpeed, Motor2_Speed = gSliderSpeed
      Serial.println("Move Forwards");

      curDir1 = HIGH;
      curDir2 = HIGH;

      if(movingBack){ //if moving back, we need to flip before moving forward
        changeSpeedSmooth(gCurSpeed1, 0, gCurSpeed2, 0, true, true);
        changeSpeedSmooth(gCurSpeed1, gSliderSpeed, gCurSpeed2, gSliderSpeed, false, false);

      }
      else{ //if turning left or turning right or moving forward, simply adjust speed on both motors
        changeSpeedSmooth(gCurSpeed1, gSliderSpeed, gCurSpeed2, gSliderSpeed, false, false);
      }

      movingBack = false;
      break;

    case 2: //Move backwards
      //goal: Motor1_Speed = -gSliderSpeed, Motor2_Speed = -gSliderSpeed
      Serial.println("Move Back");

      curDir1 = LOW;
      curDir2 = LOW;
      if(!movingBack){ //if turning left or turning right or moving forward, we need to flip before moving back
        changeSpeedSmooth(gCurSpeed1, 0, gCurSpeed2, 0, true, true);
        changeSpeedSmooth(gCurSpeed1, gSliderSpeed, gCurSpeed2, gSliderSpeed, false, false);

      }
      else{ //if moving back, simply adjust speed on both motors
        changeSpeedSmooth(gCurSpeed1, gSliderSpeed, gCurSpeed2, gSliderSpeed, false, false);
      }

      movingBack = true;
      break;

    case 3: //Turn left
      //goal: Motor1_Speed = 0, Motor2_Speed = gSliderSpeed 
      Serial.println("Turn Left");

      curDir1 = HIGH;
      curDir2 = HIGH;
      
      if(movingBack){ //if moving back, we need to flip before moving forward
        changeSpeedSmooth(gCurSpeed1, 0, gCurSpeed2, 0, true, true);
        changeSpeedSmooth(gCurSpeed1, 0, gCurSpeed2, gSliderSpeed, false, false);
      }
      else{ //if turning left or turning right or moving forward, simply adjust speed on both motors
        //increment to new speed
        changeSpeedSmooth(gCurSpeed1, 0, gCurSpeed2, gSliderSpeed, false, false);
      }

      movingBack = false;
      break;

    case 4: //Turn right
      //goal: Motor1_Speed = gSliderSpeed, Motor2_Speed = 0
      Serial.println("Turn Right");

      curDir1 = HIGH;
      curDir2 = HIGH;
      
      if(movingBack){ //if moving back, we need to flip before moving forward
        changeSpeedSmooth(gCurSpeed1, 0, gCurSpeed2, 0, true, true);
        changeSpeedSmooth(gCurSpeed1, gSliderSpeed, gCurSpeed2, 0, false, false);
      }
      else{ //if turning left or turning right or moving forward, simply adjust speed on both motors
        //increment to new speed
        changeSpeedSmooth(gCurSpeed1, gSliderSpeed, gCurSpeed2, 0, false, false);
      }

      movingBack = false;
      break;
    
    case 5: //Startup Arm
      //goal: have arm move from stable position to active position
      data = 5; //send byte protocol for arm startup to both arms
      Serial.println("Startup Arm");
      
      Wire.beginTransmission(Left_Ada_Addr);
      Wire.write(data);
      Wire.endTransmission();

      Wire.beginTransmission(Right_Ada_Addr);
      Wire.write(data);
      Wire.endTransmission();
      break;

    case 6: //Shutdown Arm
      //goal: have arm move from active position to stable position
      data = 6; //send byte protocol for arm shutdown to both arms
      Serial.println("Shutdown Arm");

      Wire.beginTransmission(Left_Ada_Addr);
      Wire.write(data);
      Wire.endTransmission();

      Wire.beginTransmission(Right_Ada_Addr);
      Wire.write(data);
      Wire.endTransmission();
      break;

    case 7: //Wave Arm
      //goal: have arm move from active position to wave, then back to active position
      //alternative which arm waves
      data = 7; //send byte protocol for arm wave to alternating arms
      Serial.println("Wave Arm");

      if(armWave){
        Wire.beginTransmission(Left_Ada_Addr);
        Wire.write(data);
        Wire.endTransmission();
      }else{
        Wire.beginTransmission(Right_Ada_Addr);
        Wire.write(data);
        Wire.endTransmission();
      }
      armWave = !armWave;
      break;

    default: //oh boi, this should not happen
       Serial.println("BUTTON VALUE ERROR");
      break;
  }
}

void speedValueHandler(BLEDevice central, BLECharacteristic speedCharacteristic){ //will run when the slider is updated to a new value on the app
  const float ratio = 255/50; //the slider operates from 0 to 50; convert to 0 to 255 for analog values
  int speedValue = (int)(*speedCharacteristic.value()); //read the value of the slider as an int
  gSliderSpeed = (speedValue * ratio);

  if(speedValue == 0) changeSpeedSmooth(gCurSpeed1, 0, gCurSpeed2, 0, false, false); //if speed is set to 0, update both motors to be 0, else wait for button press
                                                                                     //we only update the speed here if it's being set to 0
  
  // Serial.print("Updating Speed:");
  // Serial.println(gSliderSpeed);
}

void loop() {
  // put your main code here, to run repeatedly:
  
  BLE.poll(); //poll for interrupt events

  //also poll the ultrasonic sensors here, if they detect an object that's too close
}

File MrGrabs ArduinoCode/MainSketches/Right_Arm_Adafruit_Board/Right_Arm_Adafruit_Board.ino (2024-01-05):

#pragma GCC optimize ("O0")

#include <AX12A.h>

#define DirectionPin  (1u) //TX PIN
#define BaudRate    (1000000u)
#define ID_1  (1u)
#define ID_2  (2u)
#define ID_3  (3u)
#define ID_4  (4u)
#define ID_5  (5u)
#define ID_6  (6u)
#define ID_7  (7u)

#include <Wire.h>
#define Right_Ada_Addr 6
int receivedData = 0;

void setAngleLimits(){ //adjust as needed, 0 - 300 degrees
  ax12a.setAngleLimit(ID_1, 0, 1023);
  ax12a.setAngleLimit(ID_2, 0, 1023);
  ax12a.setAngleLimit(ID_3, 0, 1023);
  ax12a.setAngleLimit(ID_4, 0, 1023);
  ax12a.setAngleLimit(ID_5, 0, 1023);
  ax12a.setAngleLimit(ID_6, 0, 1023);
  ax12a.setAngleLimit(ID_7, 0, 1023);
}
void setVoltageLimits(){ //9~11V
  ax12a.setVoltageLimit(ID_1, 9, 11);
  ax12a.setVoltageLimit(ID_2, 9, 11);
  ax12a.setVoltageLimit(ID_3, 9, 11);
  ax12a.setVoltageLimit(ID_4, 9, 11);
  ax12a.setVoltageLimit(ID_5, 9, 11);
  ax12a.setVoltageLimit(ID_6, 9, 11);
  ax12a.setVoltageLimit(ID_7, 9, 11);
}
void setTorqueOn(){
  ax12a.torqueStatus(ID_1, true);
  ax12a.torqueStatus(ID_2, true);
  ax12a.torqueStatus(ID_3, true);
  ax12a.torqueStatus(ID_4, true);
  ax12a.torqueStatus(ID_5, true);
  ax12a.torqueStatus(ID_6, true);
  ax12a.torqueStatus(ID_7, true);

  ax12a.setEndless(ID_1, false);
  ax12a.setEndless(ID_2, false);
  ax12a.setEndless(ID_3, false);
  ax12a.setEndless(ID_4, false);
  ax12a.setEndless(ID_5, false);
  ax12a.setEndless(ID_6, false);
  ax12a.setEndless(ID_7, false);
}
const int complianceMargin = 15;
void setComplianceMargins(){ //10 degrees within target position
  ax12a.setCMargin(ID_1, complianceMargin, complianceMargin);
  ax12a.setCMargin(ID_2, complianceMargin, complianceMargin);
  ax12a.setCMargin(ID_3, complianceMargin, complianceMargin);
  ax12a.setCMargin(ID_4, complianceMargin, complianceMargin);
  ax12a.setCMargin(ID_5, complianceMargin, complianceMargin);
  ax12a.setCMargin(ID_6, complianceMargin, complianceMargin);
  ax12a.setCMargin(ID_7, complianceMargin, complianceMargin);
}

const int servoSpeed = 100;
void moveToState1(){ //arms stowed away
  //ax12a.moveSpeed(ID_1, 512, servoSpeed);
  ax12a.moveSpeed(ID_2, 872, servoSpeed);
  ax12a.moveSpeed(ID_3, 155, servoSpeed);
  ax12a.moveSpeed(ID_4, 218, servoSpeed);
  ax12a.moveSpeed(ID_5, 800, servoSpeed);
  ax12a.moveSpeed(ID_6, 490, servoSpeed);
  ax12a.moveSpeed(ID_7, 512, servoSpeed);
}
void moveToState2(){ //halfway lift arm up from stowed position
  //ax12a.moveSpeed(ID_1, 512, servoSpeed);
  ax12a.moveSpeed(ID_2, 679, servoSpeed);
  ax12a.moveSpeed(ID_3, 336, servoSpeed);
  ax12a.moveSpeed(ID_4, 218, servoSpeed);
  ax12a.moveSpeed(ID_5, 800, servoSpeed);
  ax12a.moveSpeed(ID_6, 490, servoSpeed);
  ax12a.moveSpeed(ID_7, 512, servoSpeed);
}
void moveToState3(){ //arm fully lifted up from stowed position
  //ax12a.moveSpeed(ID_1, 512, servoSpeed);
  ax12a.moveSpeed(ID_2, 677, servoSpeed);
  ax12a.moveSpeed(ID_3, 336, servoSpeed);
  ax12a.moveSpeed(ID_4, 317, servoSpeed);
  ax12a.moveSpeed(ID_5, 701, servoSpeed);
  ax12a.moveSpeed(ID_6, 488, servoSpeed);
  ax12a.moveSpeed(ID_7, 512, servoSpeed);
}
void moveToState4(){ //arm lower down to rest in front of computer
  //ax12a.moveSpeed(ID_1, 154, servoSpeed);
  ax12a.moveSpeed(ID_2, 692, servoSpeed);
  ax12a.moveSpeed(ID_3, 325, servoSpeed);
  ax12a.moveSpeed(ID_4, 315, servoSpeed);
  ax12a.moveSpeed(ID_5, 701, servoSpeed);
  ax12a.moveSpeed(ID_6, 491, servoSpeed);
  ax12a.moveSpeed(ID_7, 512, servoSpeed);
}
void moveToState5(){ //arm back up to rotate hand for wave preparation
  //ax12a.moveSpeed(ID_1, 512, servoSpeed);
  ax12a.moveSpeed(ID_2, 684, servoSpeed);
  ax12a.moveSpeed(ID_3, 332, servoSpeed);
  ax12a.moveSpeed(ID_4, 500, servoSpeed);
  ax12a.moveSpeed(ID_5, 509, servoSpeed);
  ax12a.moveSpeed(ID_6, 180, servoSpeed);
  ax12a.moveSpeed(ID_7, 512, servoSpeed);
}
void moveToState6(){ //move hand wave left
  //ax12a.moveSpeed(ID_1, 512, servoSpeed);
  ax12a.moveSpeed(ID_2, 685, servoSpeed);
  ax12a.moveSpeed(ID_3, 329, servoSpeed);
  ax12a.moveSpeed(ID_4, 654, servoSpeed);
  ax12a.moveSpeed(ID_5, 361, servoSpeed);
  ax12a.moveSpeed(ID_6, 180, servoSpeed);
  ax12a.moveSpeed(ID_7, 512, servoSpeed);
}
void moveToState7(){ //move hand wave right
  //ax12a.moveSpeed(ID_1, 512, servoSpeed);
  ax12a.moveSpeed(ID_2, 685, servoSpeed);
  ax12a.moveSpeed(ID_3, 328, servoSpeed);
  ax12a.moveSpeed(ID_4, 319, servoSpeed);
  ax12a.moveSpeed(ID_5, 691, servoSpeed);
  ax12a.moveSpeed(ID_6, 181, servoSpeed);
  ax12a.moveSpeed(ID_7, 512, servoSpeed);
}

void setup()
{
  Serial.begin(9600);

  Wire.begin(Right_Ada_Addr);
  Wire.onReceive(receiveEvent);

  ax12a.begin(BaudRate, DirectionPin, &Serial1);
  setTorqueOn();
  setAngleLimits();
  setVoltageLimits();
  setComplianceMargins();
}

//data is receieved in 4 bit length packets
void receiveEvent(int byteCount) {
  // Serial.println("ReceiveEvent");

  receivedData = Wire.read();

  if(receivedData == 5){
    Serial.println("Startup Arm Received");   
  }else if(receivedData == 6){
    Serial.println("Shutdown Arm Received");
  }else if(receivedData == 7){
    Serial.println("Wave Arm Received");
  }else{
    Serial.println("This should not happen");
  }
}

void loop()
{
  if(receivedData == 5){
    moveToState2();
    delay(2000);
    moveToState3();
    delay(2000);
    //moveToState4();
    //delay(2000);
  }else if(receivedData == 6){
    //shutdown
    Serial.println("Shutdown Arm Received");
    moveToState3();
    delay(2000);
    moveToState2();
    delay(2000);
    moveToState1();
  }else if(receivedData == 7){
    //wave
    moveToState5();
    delay(2000);

    int count = 0;
    do{
      moveToState6();
      delay(2000);
      moveToState7();
      delay(2000);
      count++;
    }while(count < 3);
  }
  receivedData = 0;
  delay(10);
}
